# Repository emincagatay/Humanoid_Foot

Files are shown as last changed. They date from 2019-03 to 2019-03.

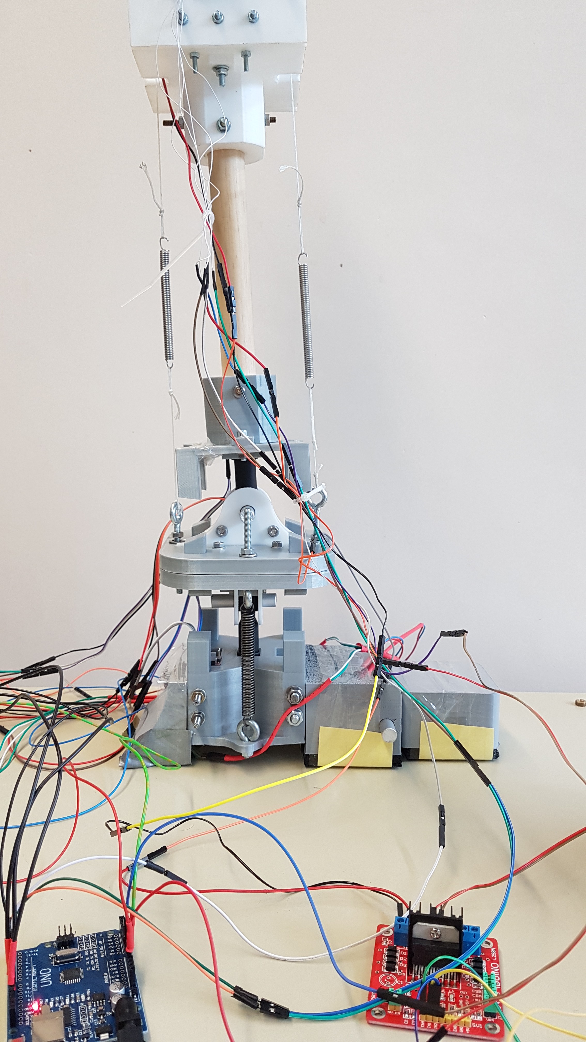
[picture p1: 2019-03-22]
Pictures/20180824_173448.jpg

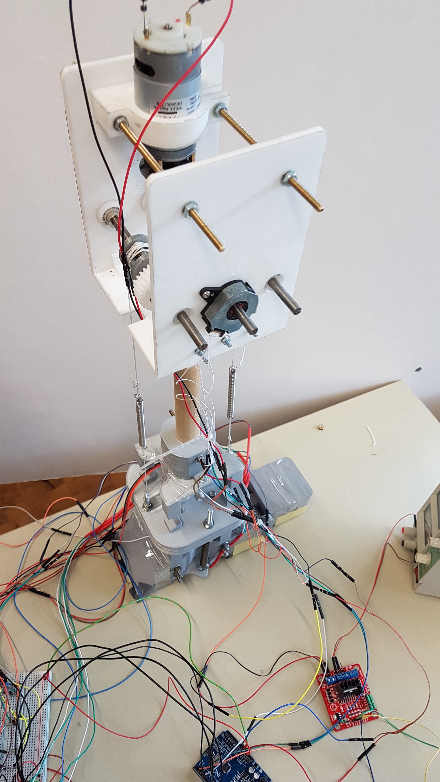
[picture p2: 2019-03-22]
Pictures/20180824_173456.jpg

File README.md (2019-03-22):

# Humanoid_Foot
Humanoid Foot Demonstrator

The project was a team project and has been completed by the team during the second semester of my Master's degree. Our project was a part of a bigger project which is the design and production of th every part of a humanoid robot and assemly of these parts. The goal of our project is the provide a starting point for a years long project. Every year new teams are asked to improve the previous version of the design. After the desired level is achieved, all parts of the robot will be assembled to form a complete humanoid robot. 

Necessary explanations can be found in the PDF-Document titled "Final Documentation for the humanoid foot demonstrator of Group 2".

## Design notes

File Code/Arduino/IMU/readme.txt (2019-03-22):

This code works with the teensy 3.6 with 3 MPU 9250 on 3 different i2c Pins with 4.7k pull up resistors. It prints the roll pitch yaw from the Earth->Sensor Transformation to the serial connection to be read by either the serial monitor/Simulink running on C/Simulink running on the Pi.
Its mostly self written but contains parts from https://github.com/arduino-ibraries/MadgwickAHRS , https://github.com/kriswiner/MPU9250 and https://github.com/nox771/i2c_t3

Interesting functionalities:
There is a I2c Scanner method which can be used to check the I2c network for devices (useful for debugging purposes). The code also includes a send2Simulink method which is used to send data to Simulink to be read via its serial read. Serial.print does not work with simulink!! But its necessary for the serial monitor. Outside of this the code should be self explanatory. If not check the sources and githubs provided for more information.

Possible Code Improvements: 
MultiThreading. currently we ask get values from one sensor before we ask the next. This process involves waiting on sensor response->multiple threads to increase efficiency
general code quality(eg enums,std::array/std::vector, etc.)
optimization for speed
EEPROM to save calibration values: currently calibration values are entered directly in the code  
Add some more method especially to access sensor setup from the main. Might be handy

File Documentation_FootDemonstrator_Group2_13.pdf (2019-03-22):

Group 2 | Humanoid foot Demonstrator | Hamburg, 26.08.2018

### Final Documentation for the humanoid foot demonstrator of Group 2

This document provides vital information and installation guides of all implemented components used in the humanoid foot. The functionality of the foot is simplified to one active pitch movement controlled with a dc motor a passive roll movement and a passive roll movement of the toes. The foot movement is detected with three IMUs, in addition an encoder is used to record rotation after the gearbox and force sensors are used to detect ground contact. The overall control is done witch a Simulink model run on a raspberry pi. The sensor data is processed with an Arduino Uno.

### Table of content

### Design

### Tasks distribution

The following table gives a brief overview of the task distribution in our group, after the design process was done.

TASK
ASSEMBLY & TESTING | Christian Brendes, Doruk Utkan, Emin Nakilcioglu, Kevin Deutmarg, Marvin
| Gravert, Stephan Hansen, Till Staude
CAD-DESIGN | Doruk Utkan, Emin Nakilcioglu, Till Staude
ENCODER | Till Staude
FORCE SENSOR | Stephan Hansen
IMU | Marvin Gravert
MOTOR CONTROL | Christian Brendes, Kevin Deutmarg
REFERENCE SIGNAL | Gunnar Maerker
SIMULINK MODEL | Christian Brendes, Kevin Deutmarg, Marvin Gravert, Stephan Hansen, Till
| Staude

### Requirement list

The requirement list was the result of an iterative design process and the base for assumptions and calculations in the part design/selection process. For further information take a look in our midterm presentation “20180518_HumRob_Midterm”.

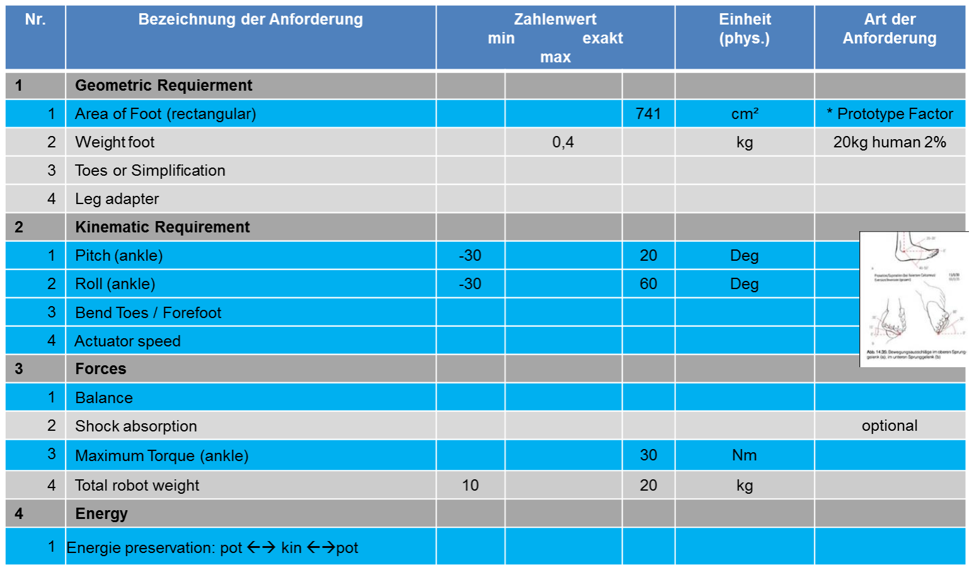
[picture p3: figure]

## Humanoid foot demonstrator Group 2

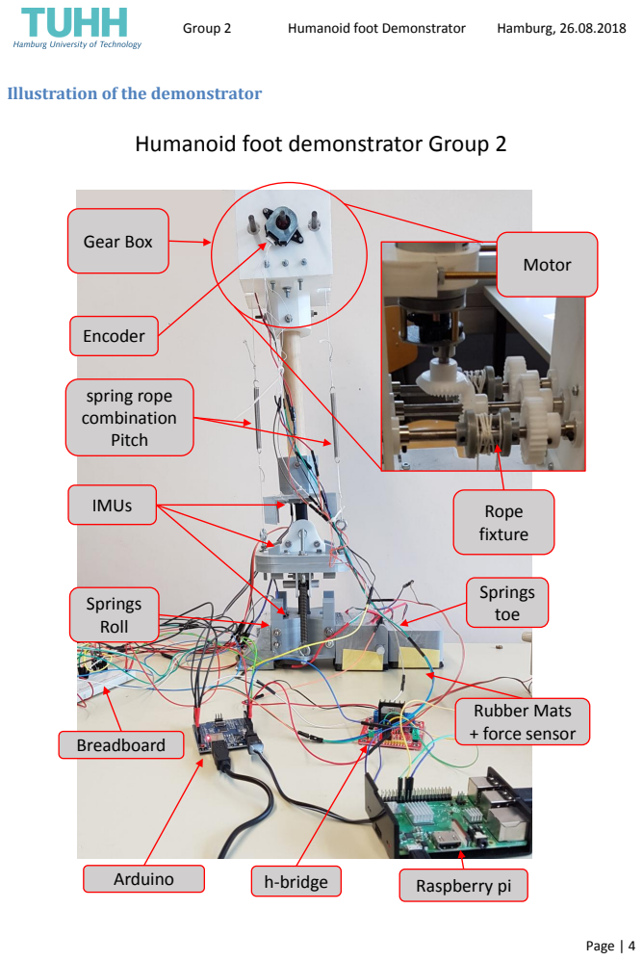
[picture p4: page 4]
Rubber Mats + force sensor; Springs Roll; spring rope combination Pitch; Encoder; Gear Box; IMUs; Breadboard; Raspberry pi Arduino; h-bridge; Motor; Rope fixture; Springs toe

Illustration of the demonstrator

### Hardware part list

The following list shows the implemented parts for this demonstrator.

Partname | Function
Raspberry Pi 3 B+ | Microcontroller for the motor control setup
H-Bridge, Iduino L298N | DC motor controller
Arduino Uno R3 | Microcontroller for processing sensor data
Teensy 3.6 | Microcontroller for processing IMU data
12V DC Motor | Actuator for the demonstrator
1x Encoder | Detect rotation of rope fixtures
3x IMUs (MPU9250) | Detect roll and pitch movement of foot
4x Interlink force sensors | Detect ground contact
2x Spring tilt
2x Spring roll
2x Spring toe
1x Bevel gear
3x Spur gear
1x A/D converter MCP3008
2x Amplifier LM 393P
Rubber mat | Adding some damping to ground contact
IGUS bearings (no. BB-626-B180-30-ES, GSR-06,
KBRM-10 OK, GBM-10, GSR-10, GFM-101115-03)
12V Power Supply Unit | Power supply for the DC motor
1x Breadboard | Used for quick wiring
RJ45 Cable, USB AtoB cable
Wires, Resistor … | Additional electrical components
Steel shaft, screws, … | Mechanical components for assembly

### Assembly Instructions for the current state

The foot is stored half-assembled right now. All small wires are connected and most mechanical parts are in place. If you want to put the foot together, only the following steps are needed:

Mechanical Assembly
- put together the bearing and shaft for pitch
- attach roll springs, tight the screws such that roll is in balance
- attach pitch springs, tight the screws that pitch is in balance
Electronic Assembly
- connect the Arduino to the Raspberry via USB (B to A) using the upper left USB port
- connect the Teensy to the Raspberry via USB (Micro-B to A) using the lower left USB port
- connect the Arduino and Raspberry to their power supplies
- connect the H-bridge to a power supply (12V)
- connect the Raspberry via Ethernet to your PC running Simulink

### Exploded view of the CAD Model

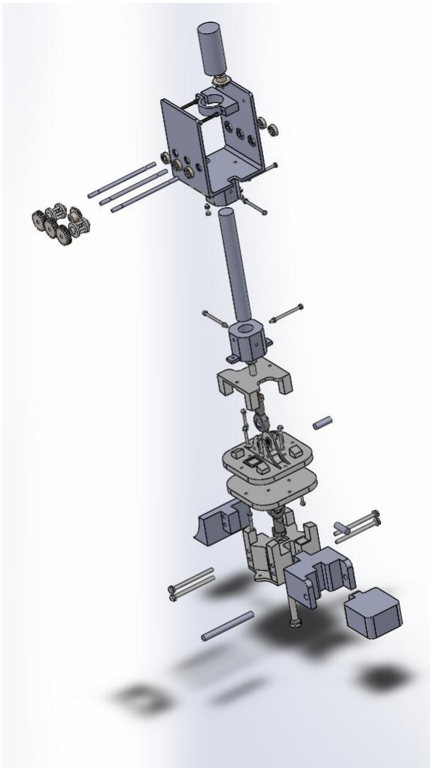
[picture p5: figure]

### Model for Pitch Behavior

We created a simple model for the pitch behavior which may help as a start for control purposes.Please find the illustrations and calculations in a separate file: Attachment_Pitch_Model.docx

The model has not been tested in further detail but it has been implemented in matlab/Simulink and can be found in the folder Attachment_Pitch_Model

### Selection of components

### Selection of Roll Springs (Extension Springs)

Aim: Find springs such that the roll of up to +/-30° happens with relatively little resistance (1-2Nm) estimated by body weight and leverage when ground contact is not centered below the foot. [I’d recommend to reestimate the value in a next iteration]

Link to shop:
https://www.febrotec.de/content.php?seite=shop/produkte.php&details=16226&hauptrubrik=23

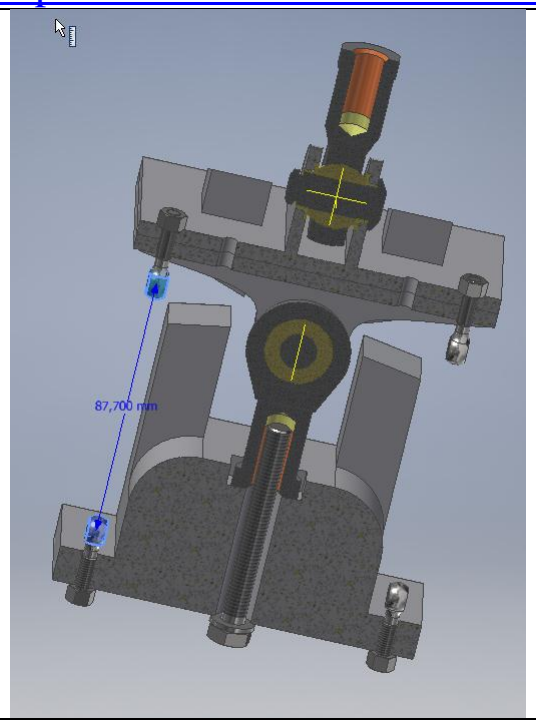
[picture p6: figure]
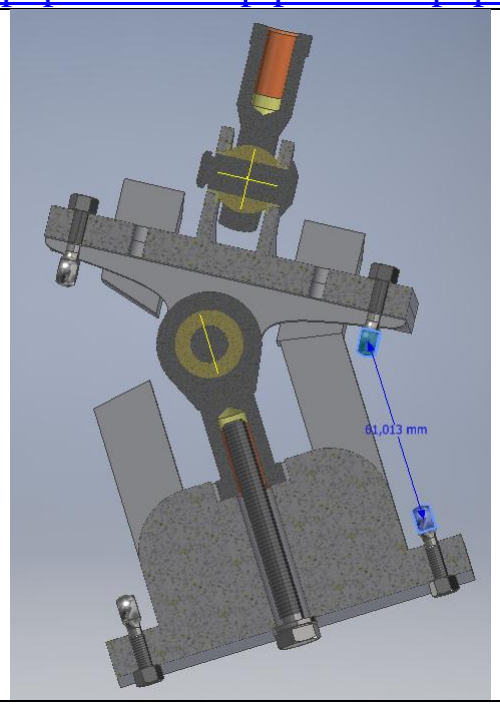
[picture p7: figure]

Zero Position | At 30° (max angle) | At -30° (min angle)
Spring length over angle | Force in spring over angle | Moment of both springs about rotation axis over angle → see what angle is achieved by which external moment

Find in files: RollSpringDiagram.mlx → Code for calculations

### Selection of Pitch Springs (Extension Springs)

For selected spring rotation of motor (beta) and pitch angle (alpha) and corresponding moment over pitch axis. (These values are independent of the roll angle!)

Note: We selected rather hugh springs as we initially planned to support big moments which may be necessary for walking (30/40 Nm). During the design we finally assumed our prototype would not manage the big pretension forces caused by these springs, so finally they were not used. For the next iteration in design, either design a more stable component (problem: expensive, harder to manufacture) or choose smaller springs and assume smaller load values (i.e. moments).

Find in files: PitchSpringDiagram.mlx → Code for calculations

Troubleshooting:
The selected (and bought) springs were way too massive to be implemented in the current system, since the prototype could probably not withstand the loads assumed for a full (child sized) human. So we did finally decide to not use the spring but users we got in the workshop. In the next iteration change the size of the components (some were oversized, others were too small) to fit the expected loads.

### Selection of Actuator

To select a suitable actuator for the pitch movement initial calculation were necessary to get a number for the motor power and rotational speed. The following table contain the Power calculation of our motor. Therefore simplified assumptions of the overall dimensions of our foot design were made, illustrated in Figure 1.

Foot Moment | 30 Nm -> requirement list
Foot Mass | 3000 g (see figure .. for dimension) | Density 1.5 g/cm³ 3D-Printer Material
Inertia | = 0.0275 kg*m²
Spring Force | 30 Nm / 0.05m = 600N

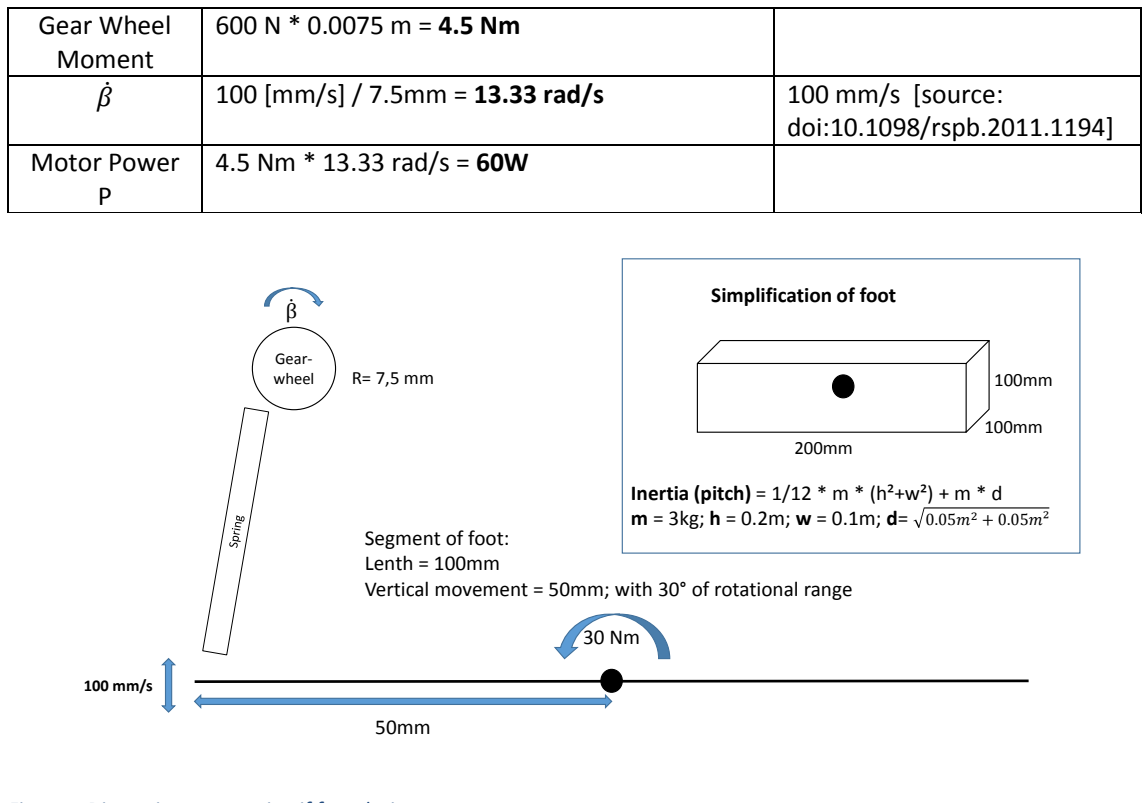
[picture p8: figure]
Gear-; wheel; Segment of foot: Lenth = 100mm; Simplification of foot

Gear Wheel Moment | 600 N * 0.0075 m = 4.5 Nm
β̇ | 100 [mm/s] / 7.5mm = 13.33 rad/s | 100 mm/s [source: doi:10.1098/rspb.2011.1194]
Motor Power P | 4.5 Nm * 13.33 rad/s = 60W

Figure 1 Dimension assumption if foot design

With this rather conservative calculation we come to the solution that we require 60W of Motor Power. The following internet search for a suitable motors concluded we have to lower the requirements for the motor to fit it in to our budget of 300€

If we lower our torque requirement from 30 Nm to 15Nm and also changing and change our speed from 100mm/s to 50mm/s we end up with a gear moment of 2,25Nm and 63,6RPM. That is almost in the range of the following motor! (Hochleistungsgetriebemotor 12 V Modelcraft RB350050-22723R 50:1 https://www.conrad.de/de/hochleistungsgetriebemotor-12-v-modelcraft-rb350050-22723r-501-233132.html (https://www.conrad.de/de/hochleistungsgetriebemotor-12-v-modelcraft-rb350050-22723r-501-233132.html) )

Vertical movement = 50mm; with 30° of rotational range

Inertia (pitch) = 1/12 * m * (h²+w²) + m * d m = 3kg; h = 0.2m; w = 0.1m; d=

### Design Process of the Gearbox, Toes and Heel

Gearbox includes a motor mount, a framework, 6 ball bearings, 1 bevel gears set, 3 spur gears and 2 winders. Taking into account the torque that needs to be transferred, the modules of the gears, diameter of the shafts and dimensions of the ball bearings have been calculated. Bevel gears and spur gears requires the module of at least 0,58 and 0,8, respectively.

Determining the Shaft Diameter
Torsion occurred on the shaft by DC Motor;

P = 1 ,18 W , n = 44,18 rp (taken from the DC motor catalogue considering the torque of 3,28 Nm)

τb1 =

16 ∗ M1
π ∗ d1

3 ≤ τem = 72 MPa

M1 = 9

P
n

= 3,28 N

d1

3 ≥

16 ∗ 3,28
π ∗ 72

→ d1 ≥ 2,8

Forces acting on the spur gears;

Ft2 = Ft3 =

2 ∗ T
d

= 218,6 N

Fr2 = Fr3 = Ft ∗ tan α = 79, 6 N

Forces acting on the bevel gears;

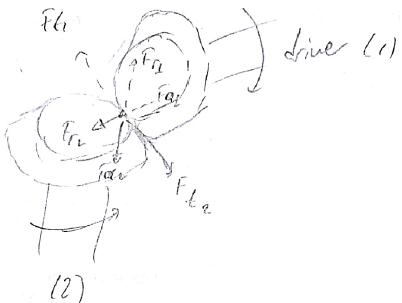
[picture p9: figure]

Reference cone angles (δ1, δ )= 45°, helix angle (β )= 0° ,shaft angle(∑) = 90°

pressure angle (α) = 20° , face width(b) = 7 mm , dm= reference diameter angle

dm1 = 31 − 7 ∗ sin δ1 = 26,

dm2 = 31 − 7 ∗ sin δ = 26,

Ft1 = Ft2

Ft1 =

2 ∗ T dm
= 218,6 N

Fr2 = Fa1 = Ft ∗ tan α ∗ sin δ = 64,81 N

Fr1 = Fa2 = Ft ∗ tan α ∗ cos δ = 64,81 N

a = 33,7 | , b = 16 | , c = 14,3

Mtorsion = 3,28 N

Mbending = Mx = −Fr2

∗ (a | b | 18) Fa2
∗ 26, | ≈ −2,7 N

According to the maximum shear stress theory;

Meq = √Mt
Mb

2
= 4,24 N

d1

3 ≥

32 ∗ Meq
π ∗ τem

→ d1 ≥ 3,91

6 mm has been decided as the shaft diameter considering the safety factor of 1,5.

After these calculations, we have bought gears made of Polyacetal, which meets the design criteria, silver shafts with 6 mm diameter and ball bearing with plastic cage material and balls made of stainless steel. Winders which plays the active role in the transmission was designed in the shape of a cylindrical cage so that during the assembly rope could have been easily fixed onto one of the bars regardless of the initial position of the winder. Framework, motor mount and the winders has been printed using 3D Printer.

The toes and heel parts are connected to lower adapter part in a way that lower adapter part is a bit elevated from the ground. There are 2 reasons for this setup: Main reason is to imitate the arc structure of the foot in human beings. Scientific papers show that the middle part of the foot has the lowest pressure while walking or standing and the most pressured points are the toes and heels. The second reason is due to the screws in the lower adapter part which should not contact to the ground as it would disturb the contact layer of the foot.2 torsional springs are used to imitate the bending of toes so that some of the energy can be restored and reused passively while walking.

Troubleshooting
The 3d printing process of toes and heels were a bit frustrating. At first trial 100% printing density was used but the parts were too heavy for the motor to handle. At second trial 30% is used but this time the quality of the parts was poor therefore the parts had to be reprinted many times which is very frustrating and suffering since the printing time was quite long and the student workshop was unexpectedly closed some days during the course of the semester.

### Actuator - 12V DC Motor

This is the installation guide our human foot demonstrator. This part provides the installation steps for creating a DC motor control with an H-Bridge and Raspberry Pi 3 B+ and MATLAB Simulink R2018a. It covers the following:

- Used hardware part list
- Schematic of all components
- Flashing procedure of the Pi with MATLAB OS
- Network configuration for communication setup
- Manual for the motor control MATLAB script
- Manual for the motor driver in Simulink

### Used hardware part list

The following list shows the used parts for this motor setup for this demonstrator.

Partname | Function
Raspberry Pi 3 B+ | Microcontroller for the motor control setup
H-Bridge, Iduino L298N | DC motor controller
12V DC Motor | Actuator for the demonstrator
12V Power Supply Unit | Power supply for the DC motor
Breadboard | Used for quick wiring
Breadboard cables | Connectors for quick wiring
3x LEDs | Used for indicating the current status of the motor (turn left, turn right, stop)
Micro USB Power Supply Unit | Power cord for the microcontroller
RJ45 Cable, 1m | Network cable for connecting Pi with PC
3x resistors | Required for the lowering the input voltage of LED

### Schematic of all components

The schematic of the demonstrator is straight forward. Pi 3 B+ we use the following GPIO pin layout as reference.

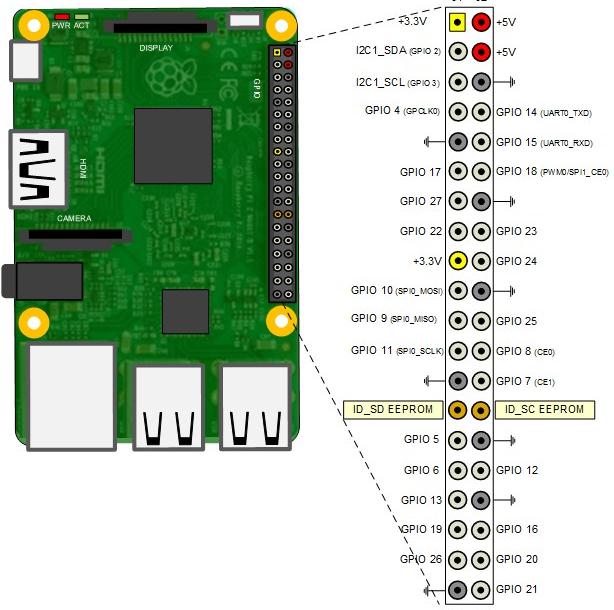
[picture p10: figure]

Figure 2 MATLAB showPins layout for Pi Model 3 B

From the Pi we use ground and map it on the breadboard for our LED monitoring. The LEDs need a dropping resistor otherwise the LED would break, since the output voltage of the GPIO pins are 3.3V and the permitted voltage for LEDs we have used is 1.6V. Constants:

UGPIO = 3 3 V

IGPIO = 16 A

ULED = 2 V

RV =

UGPIO − ULED

IGPIO

=

3 3 V − 1 6 V
16 A

= 1 6 2 Ω

Therefore, we chose the next bigger available resistor which has a resistance of 110 Ω.

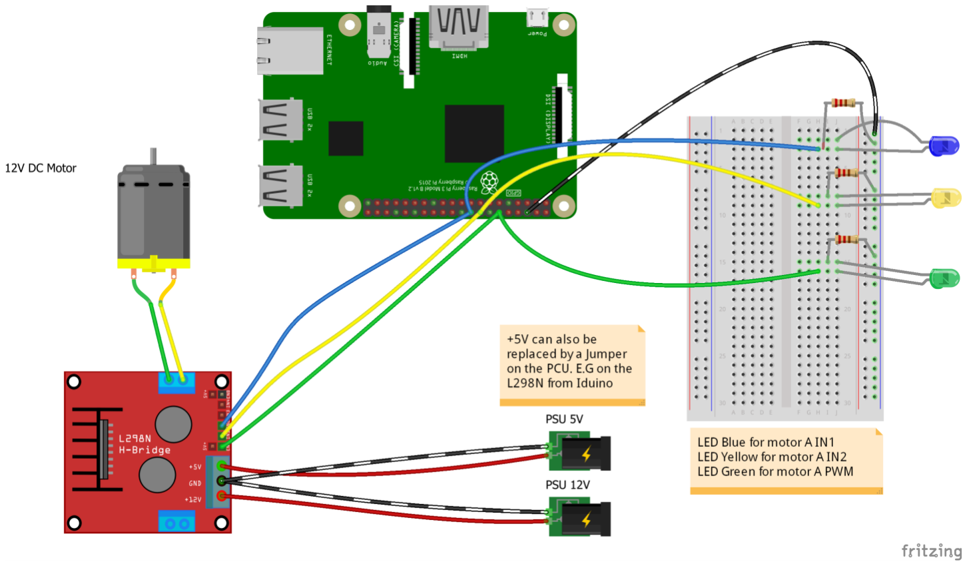
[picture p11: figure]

Figure 3 Fritzing Breadboard Diagramm for Motor Control

From the Pi we connect the breadboard LED control with series resistors. Use therefore ground, GPIO 18 for green, GPIO 23 for yellow and GPIO 24 blue.

Next we connect the Pi with the H-Bridge. Simply connect the GPIO 18 to Enable A (EnA control for motor A, we could control also two motors with this bridge). This allows us the control the motor speed with Pulse Width Modulation (PWM). Then connect GPIO 23 for IN2 and 24 for IN3.

In order to understand the way of controlling the motor we visualize the small motor control.

InA | InB | Motor movement
0 | 0 | Stop
0 | 1 | Left
1 | 0 | Right
1 | 1 | Stop
Table 1 Motor Control

Now we hook up the motor by using the corresponding motor pins for voltage and ground. Since we have a DC motor it doesn’t matter in with order we connect power or ground, it only affects the way of turning the motor. So be consistent and test afterwards which way the motor is turning depending on your input of InA and InB.

Lastly we need to connect power to the H-bridge. Depending on the purchased model a jumper will be shipped. The purpose of the jumper is to use 5V of the 12V power needed for the motor to supply the onboard components of the bridge with power to work properly. If you remove the jumper you need to attach a separate 5V power supply to power up the board and additional 12V for the motor power supply.

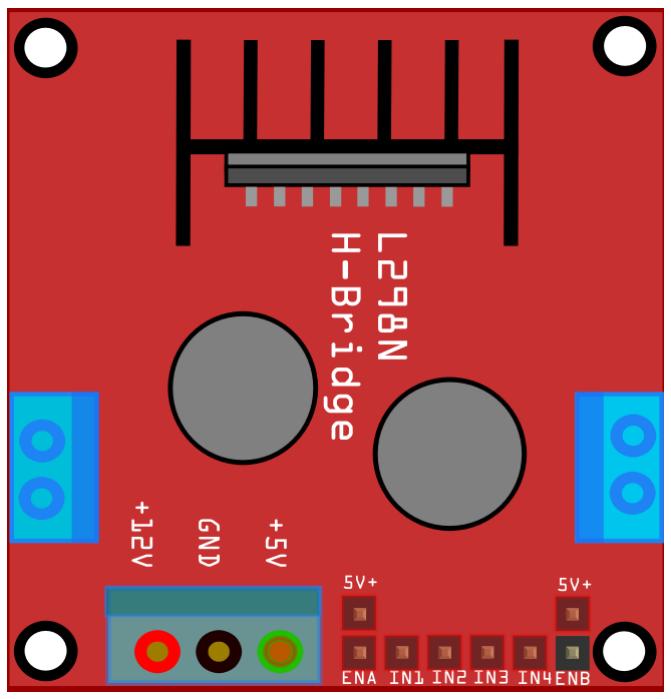
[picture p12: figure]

Figure 4 H-Bridge

Troubleshooting
Depending on the used power supply, place the jumper to power on the board, otherwise the board won’t receive signals from the microcontroller.

### Sensors

This section gives a brief description of the implemented sensors

### Encoder

The Encoder (AMT31 by CUI INC) is used to read the angle of the middle gear shaft. This corresponds (1:1) to the motor angle (behind the gear which is purchased with the motor). The connector “JAE FI-W17S” was not easily available, so we build our own, only connecting to pins 4,6,8,10,12, corresponding to GND, +5V, B+, A+, Z+.

The following Figure 5 gives the wiring and the corresponding pins

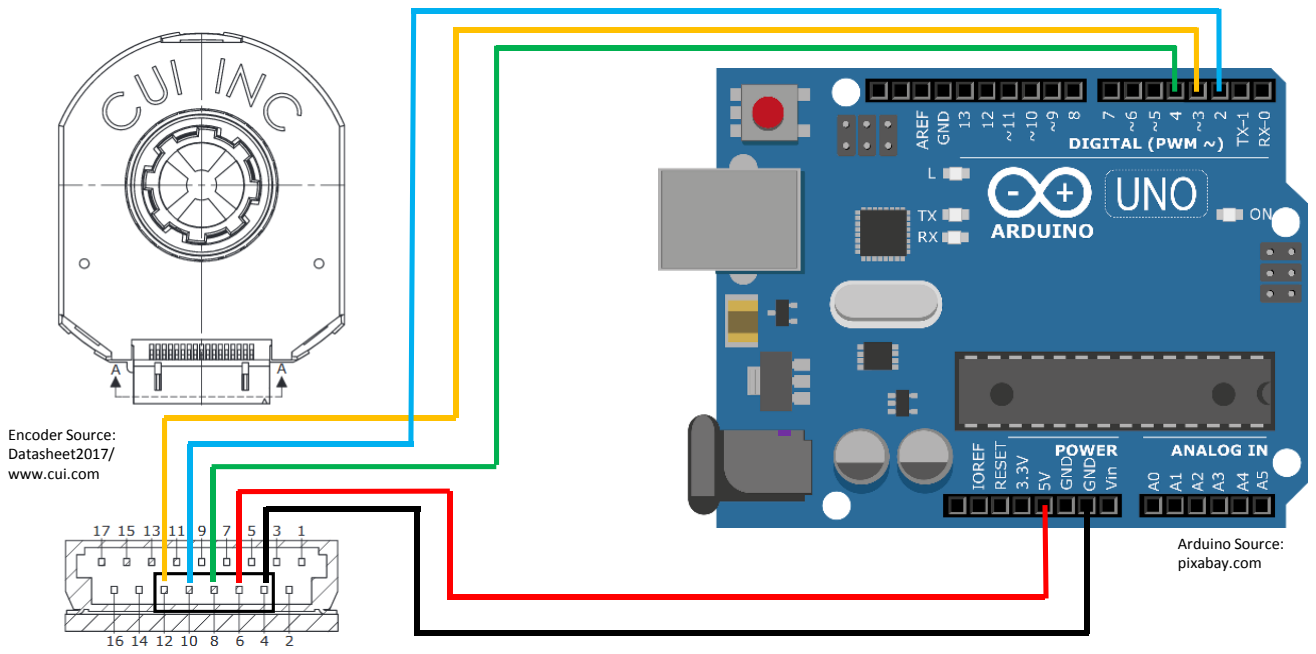
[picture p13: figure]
Arduino Source: pixabay.com; Encoder Source: Datasheet2017/ www.cui.com

Figure 5 Wiring Encoder Arduino

A & B form a quadrature signal. They are the same signal but shifted in time. If A lags behind be the rotation direction is the one way (say negative), if B legs behind A it is the other direction (say positive). There is four cases when a change in A (or B) was detected A=1 & B=0; A=0 & B=1 (both positive direction) and A=0 & B=1; A=1 & B=0 (both negative direction).

Z gives a pulse whenever a zero crossing happens.

As the encoder works incremental each signal flank of either A or B must be detected to correctly sum the steps to the angular value. The encoder resolution is 4096/round (so 2048 up and 2048 down flanks). Using Simulink for Raspberry Pi we could not read the data sufficiently fast (especially when other blocks like the motor control were included) thus we moved the encoder reading to a Arduino and only send the calculated angular value via a serial connection (USB).

To always reference to the same 0 position (given by Z signal) we initially turn the motor slowly until the first Z pulse is received, only after that that initialized bit is set and the actual code may start. (Note: make sure the motor is in the correct rotation, as this cannot be detected by the encoder and initially rotation 0 is always assumed.)

For the serial connection, set the correct Port in the Simulink Block, find the value by typing

ls /dev/tty*
in the command line on the paspberry pi (e.g using putty) and see which element is added when you connect the Arduino by USB.

Find in the files:

Data sheet of encoder; Code for Arduino

Troubleshooting:
The encoder seemed to “pass out” at times, we are not sure for the reason, but we did not even get a signal using an oscilloscope. Possible reasons may be: Bad connector, loose connection, insufficient power supply by the Arduino, bad quality of the encoder or anything else.

### Force Sensor

The force sensor (Interlink Drucksensor Force-Sensing Resistor FSR) are used to detect whether the foot is touching the ground or not. These sensors are passive elements exhibits a decrease in resistance when there is an increase in the force. The dimensions of the sensors are 18.3 x 0.46 mm(Ø x H) and have a working range from 0.2N – 20N. A typical resistance vs. force curve is shown in Figure 6 Force to Resistance and Voltage relationship of FSR; source: FSR® Integration Guide.

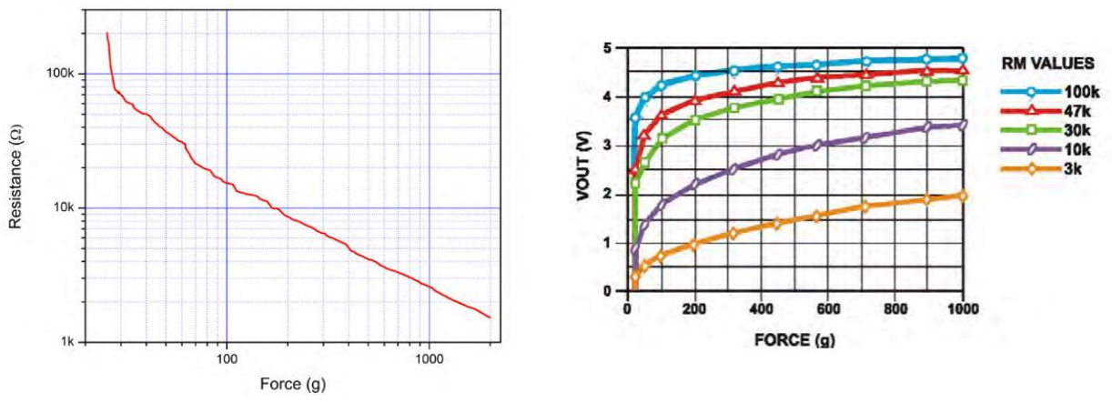
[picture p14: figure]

Figure 6 Force to Resistance and Voltage relationship of FSR; source: FSR® Integration Guide

The measurement setup is shown in Figure 7, a simple voltage divider circuit including the FSR Resistor is used. In the shown configuration, the output voltage increases with increasing force. The measuring resistor, RM, is chosen to maximize the desired force sensitivity range and to limit current. In our implementation RM is chosen as 57 kΩ. As amplifier the LM 393P is used, for further information check the data sheet (http://www.ti.com/lit/ds/symlink/lm393.pdf).

Figure 7

To convert the analog signal given by Vout to a digital signal the MCP 3008 is used. The MCP3008 device is a 10-bit Analog-to-Digital (A/D) converter with on-board sample and hold circuitry, it operates over a broad voltage range (2.7V - 5.5V). Our operation range is the 3.3V output from the Arduino Uno R3. The MCP 3008 has 8 input channel, we only need 4 channel, the wiring to the Arduino is shown in Figure 8. The communication is done via the spi interface. To read out channel 0-3 we followed the tutorial from Robert Fromm (http://www.robert-fromm.info/?post=elec_spi_mcp3008), also used his code.

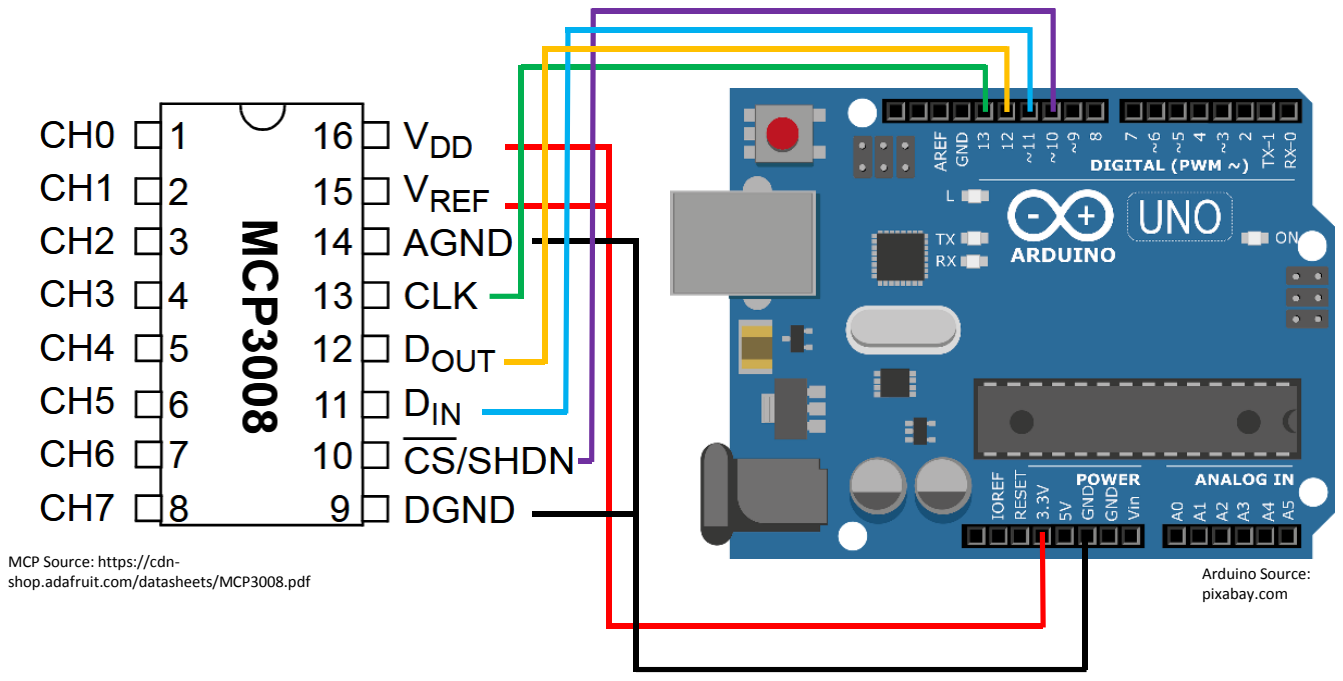
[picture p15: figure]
Arduino Source: pixabay.com; MCP Source: https://cdn-

Figure 8 MCP3008 to Arduino wiring

Vout

V (3,3V)

GND

Vout =

V
( | )

shop.adafruit.com/datasheets/MCP3008.pdf

Troubleshooting: To detect the ground contact more reliable a small paper was placed under the Force sensors

### IMU

Reason to use IMUs: For the control loop it is necessary to calculate the pitch and roll. This can obviously be achieved using encoders, but they are quite expensive. Therefore we wanted to try out the cheaper IMUs. They are used to calculate the roll pitch (yaw) between the earth frame and the sensor frame. This can in turn be used to calculate the relative angle between them.

For 1 DOF joints this is achievable with only 6 axis IMUs (gyroscope+accelerometer) assuming the sensor axis allign with the axis of rotation (or the transformation is known). For a more general and theoretically more robust method we decided on 9 axis IMU (also includes an magnometer).

Choice of Hardware: We decided to use the MPU9250 from Invensense due to its cheap price and its frequent use in the open source community, therefore offering a good basis in case of problems to fall back on. In the sources folder you find the product information, register map as well the orientation of the MPU.

Note that we didnt buy the MPU9250 directly but rather bought a breakout board for its ease of use.

To run the sensor fusion we orginally wanted to use a Raspberry Pi but run into some problems with simulink and first turned to the Arduino UNO. While we got the fusion (somewhat, see below) working for one sensor, we figured the UNO is still to slow to offer results in the acceptable range. Hence we used a Teensy 3.6. Its more than ten times faster than an UNO and offers 4 I2Cs Channels/Ports/Pins.

Senor Fusion: As already remarked we orginally thought of the using the Raspberry Pi. This would have probably resulted in quite a low sampling rate. Hence we looked for a sensor fusion still offering acceptable results at low rates who would also be computationally inexpensive. The fusion algorithm designed by Magdwick fits the pill (paper in sources, http://x-io.co.uk/open-source-imu-and-ahrsalgorithms/ ).

Calibration: In theory all individual sensors on the MPU9250 (acc, gyro, mag) have to be calibrated. In practise we have only calibrated the offset in the gyroscope(absolutly necessary) and the scaling error as well offset magnometer (absolutly necessary). For the first we simply took x amounts of samples while the gyros werent moved and averaged it to calculate the offset. The scaling error couldnt be calibrated, because we were lacking a reference angluar velocity. The magnometer calibration is very important. There exist quite a few ways to this. We went with a simple mapping as described here (https://github.com/kriswiner/MPU6050/wiki/Simple-and-Effective-Magnetometer-Calibration ). Most simple magnometer calibration rely on mapping ellipsoid measurements to a sphere (for one see sources). At this point its important to note that our magnometer wasnt well calibrated and we experienced poor performance due to it. So you would be well advised to look for other calibration methods.

Set Up: The Teensy is connected to the Raspberry/PC over a micro USB cable. The sensor are connected to the 3.3V and Ground of the teensy. Each indiviual IMU is connected to an I2c channel of the teensy. Furthermore 4.7k pull up resistors have to used (This is a must, otherwise you wont get readings).

Code: The code was written for the teensy but its close to known Arudino libaries. Its recommended to know some C++. Furthermore you will have to install teensyduino.

Performance: We had good results for the roll and pitch but pretty bad ones for the yaw. We believe this is due to the insufficient calibration.

Troubleshooting:

### Matlab/Simulink

### Flashing procedure of the Pi with MATLAB OS

There are two options to flash the SD card with the raspbian operating system including all packages from matlab.

Option 1 – Tutorial via Matlab

There exists a tutorial provided by Matlab to set up your raspberry pi. If this works great! otherwise turn

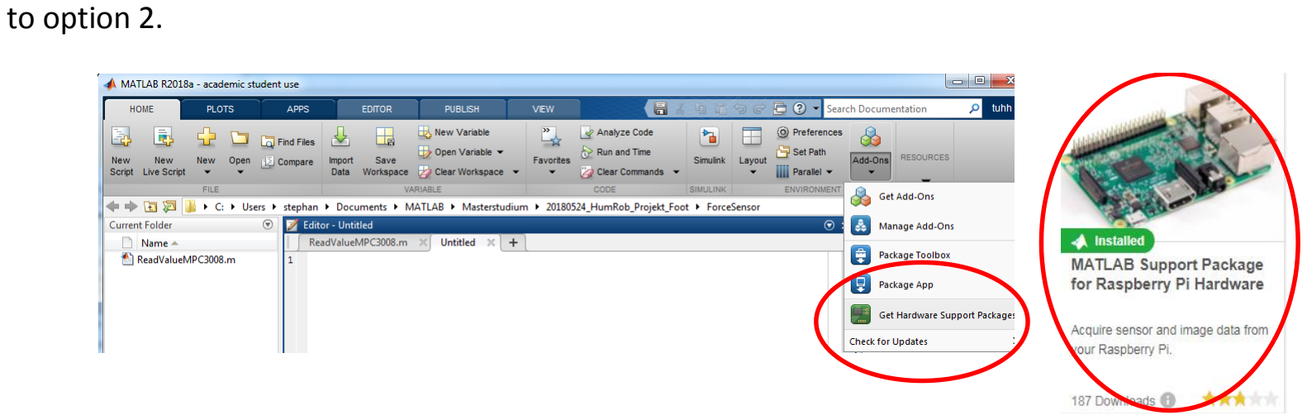
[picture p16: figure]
to option 2.

Note: The raspbian op provided by matlab was not bootable with the raspberry pi model 3b+

Option 2 – Manual installation

Firstly download the newest version of raspbian op
(https://www.raspberrypi.org/downloads/raspbian/), this should guarantee to work with your raspberry pi. Afterwards flash your SD card with the downloaded op (Hint: We used Win32 Disk Imager). Insert the SD Card in your pi and boot the op system. Make sure you have installed all updates, therefore enter sudo raspi-config into the console.

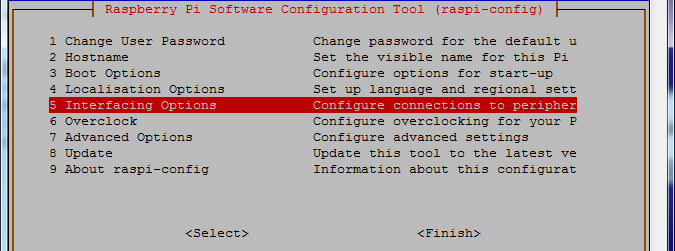
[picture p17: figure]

Abbildung 1 Source: https://learn.adafruit.com/adafruits-raspberry-pi-lesson-4-gpio-setup/configuring-i2c

Under 8.Advanced Options the raspberry pi can be updated. Afterwards reboot and install the missing matlab packages with the following command.

sudo apt-get install matlab-rpi

If the installation was successful run sudo raspi-config and select 5.Interfacing Options, enable ssh, i2c and gpio connection. Afterwards reboot your pi and connect it to your pc via a lan-cable. Make sure you know the IPaddress of your pi. Run sudo ifconfig to find the IP address next to the wlan0 entry. At last run the rasp(‘IP-Adress’,’user name’,’password’) command in matlab.

To verify the installation reinstall the Matlab Support Package for Raspberry Pi Hardware witch Matlab on an existing operating system.

Troubleshooting

If the installation of the matlab packages was not possible in one step there is the option to install the packages one by one. Also note you have to run the command rasp(‘IP-Adress’,’user name’,’password’) at least once before you can verify your installation with the “Matlab Support Package for Raspberry Pi Hardware”.

One by one installation: run the following command and replace the xxx with the listed package names

sudo apt-get install xxx

libsdl1.2-dev | alsa-utils | espeak | i2c-tools
libi2c-dev | ssmtp | ntpdate | git-core
v4l-utils | cmake | sense-hat | sox
libsox-fmt-all | libsox-dev | libcurl4-openssl-dev

### Network configuration for communication setup

During the flashing of the raspberry Pi one was asked to define a proper IP address to the PI. We have chosen: 169.254.0.2.

After that we need to hook up the PI with our PC using the Ethernet cable. Then we need to re-configure our network IPv4 address to: 169.254.0.10 / 255.255.0.0

Once this is done we can start Matlab to run our setup code.

### Manual for the motor control MATLAB script

As a pre-reqiusited for using matlab on raspberry pi you need to install the current support packages for matlab and Simulink, which can be easily found via Get Hardware Support Packages.

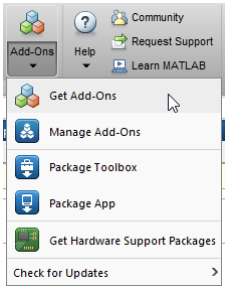
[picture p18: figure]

Then install Simulink support package for raspberry pi hardware and matlab support package for raspberry pi hardware.

Via installation follow the instructions of the install wizard and you good to go.

For the motor control we have set up a dedicated matlab script for initial testing. Within there we have placed additional comments for easy understanding of the functions from the MATLAB raspberry PI API.

An overview of the function used can be found on following link: https://de.mathworks.com/help/supportpkg/raspberrypiio/functionlist.html

### Manual for the motor driver in Simulink

Within Simulink we have created a motor control block which takes and input u which can be between [-1,1]. This input should come from another system block which provides new directives turning or stopping the motor. Output signals are pwm_out (for motor speed), mIn1_ and ,In2_out for the turning and stopping the motor.

The control scheme looks as follows:

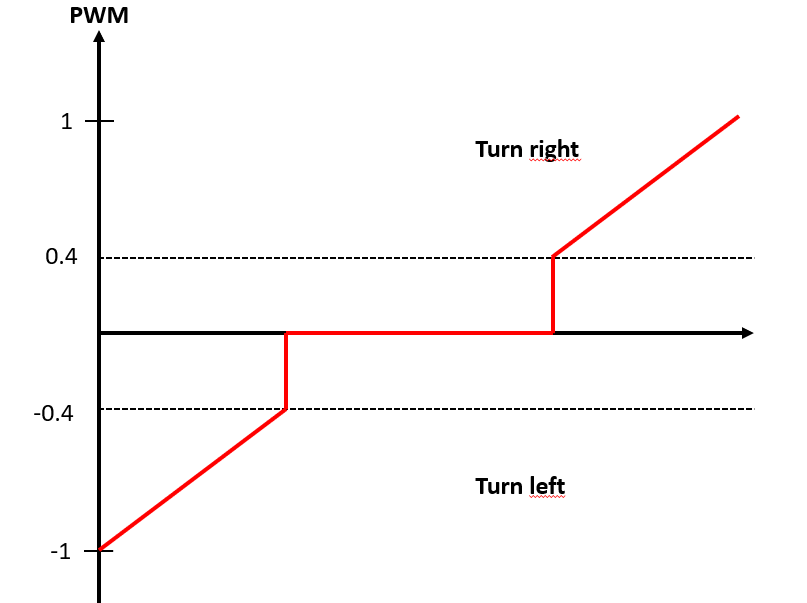
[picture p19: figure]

Before running the simulation check first if the simulation is selected to external. Otherwise you won’t be able to see anything in your scope when you would like to check some signals.

### Reference Signal for the ankle

According to Kwons and Parks paper "Kinesiology-based robot foot design for human-like walking." from 2012, the foot movement happens in four phases:
1. Standing (PHI = 0, foot has full ground contact)
2. Take-off (PHI > 0, PHI increases, foot has some ground contact)
3. Swing (PHI decreases, foot is in the air)
4. Landing (PHI < 0, PHI increases, foot has some ground contact) (This numbering conforms the one in Simulink.)

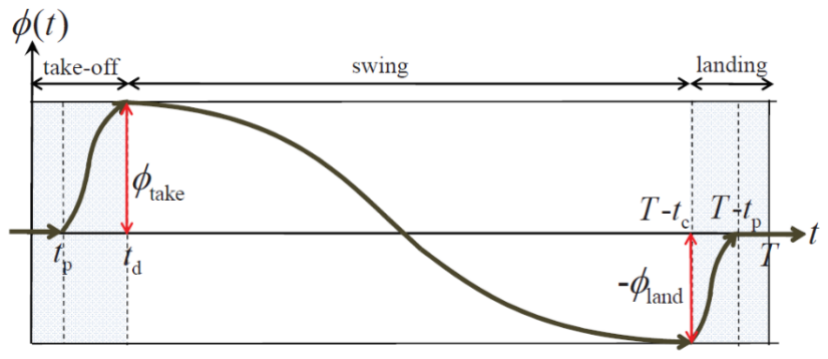
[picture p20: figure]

To be able to start off with slower movements, a scaling factor is used. If it’s set to one, T equals the suggested value of 2 seconds. The Simulink model which provides this curve looks like this:

The Time-Subsystem counts the time of a phase in seconds and provides it as a variable for the Function Subsystem, where the functions of all 4 phases are being calculated. The multiport switch then picks the right function based on the phase which is actually happening. This information comes from the phase no counter subsystem. For more insights look into the documentation of this.

### Overall Control Model

In the following segment some general remarks for the Simulink model for the demonstrator will be made. The model will be introduced in the following graphic.

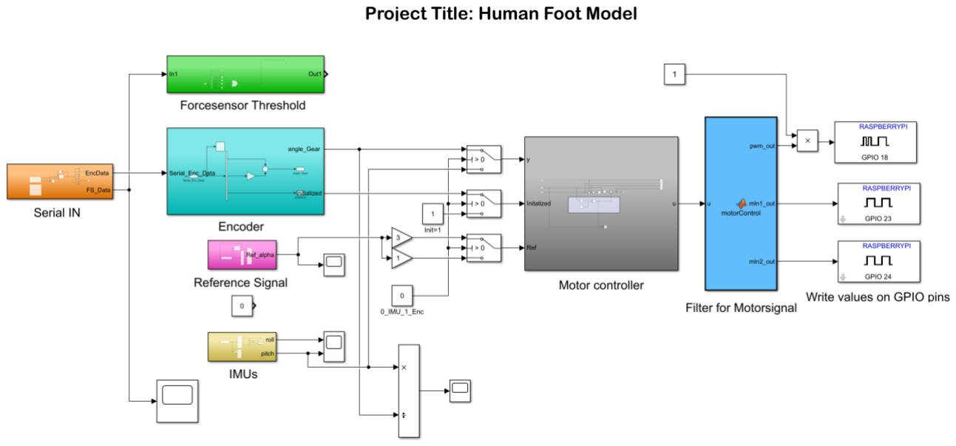
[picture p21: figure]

The model contains blocks to read out data from the different sensors, control the motor and to write the values of the motor controller onto the GPIO pins of the raspberry pi. It starts with a “Serial IN” block which is used to read out the data from the force sensors and the encoder (which are both preprocessed on the Arduino) over the USB port of the raspberry pi (connected to the Arduino). The block diagram looks as followed.

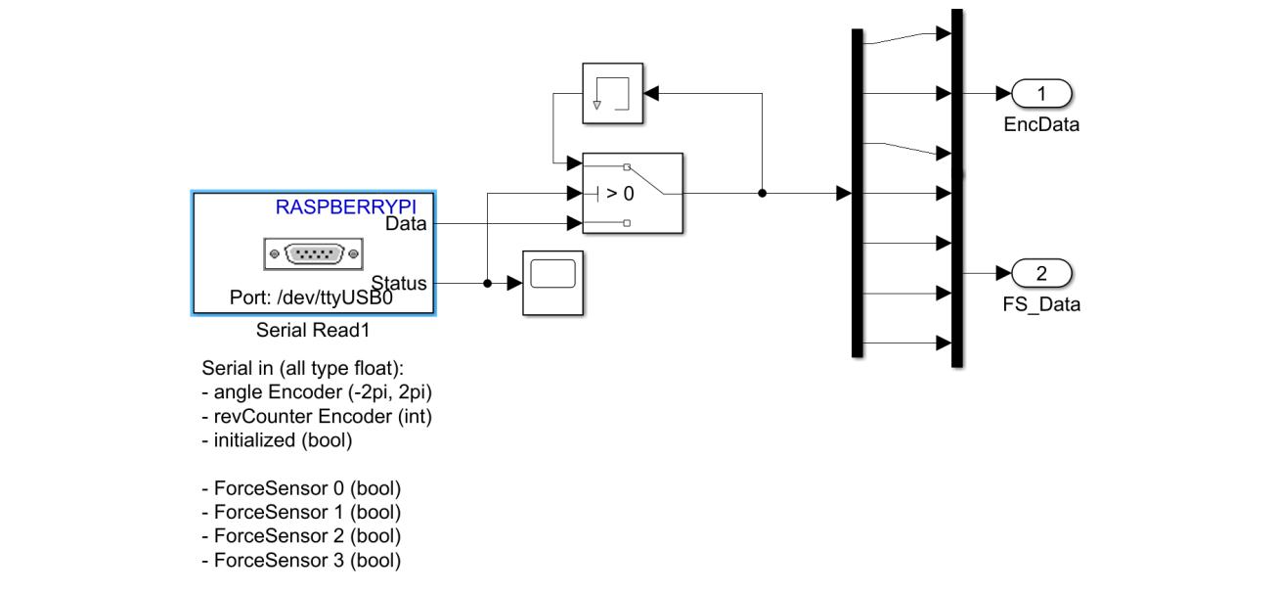
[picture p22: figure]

The “Serial IN” block is followed by the “Force sensor Threshold” and the “Encoder” blocks which are used to process the acquired data. The force sensors are so far only used to determine whether the foot touches the ground or not which is used to trigger the movement of the foot.

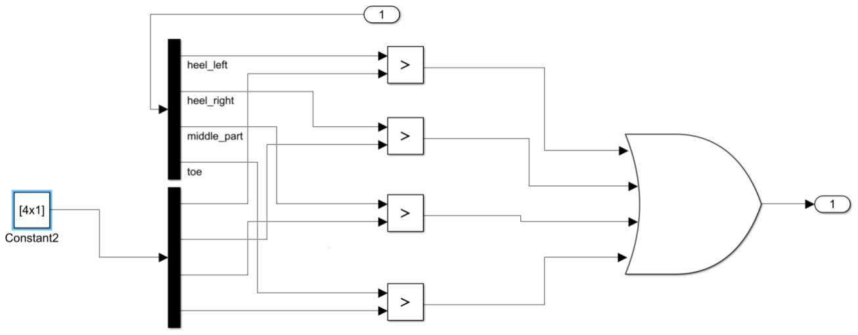
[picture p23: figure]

Here the input vector from the sensors gets demuxed and compared to a distinct value which is one since we are only detecting whether the foot is in contact with the ground or not. Therefore, if one of the sensors give a value greater than 1, the foot is in contact with the ground and the output of the block will be a logical 1 which is supposed to trigger the foot motion in future projects.

The “Serial IN” also delivers an input for the encoder block, which is illustrated in the following picture.

Here the collected data (see the previous Encoder section) will be demuxed. The data vector contains the following information:

1. The angle of the foot in an interval of (-2pi; 2pi)
2. The full revolutions counted (using the encoders Z signal)
3. A flag indicating if the encoder is initialized (i.e. at least one zero crossing was registered before)

The full angle is calculated by adding the current angle to the 2pi multiple of the revolution counter.

The reference signal block is described in the previous subchapter and additionally documented in the code.

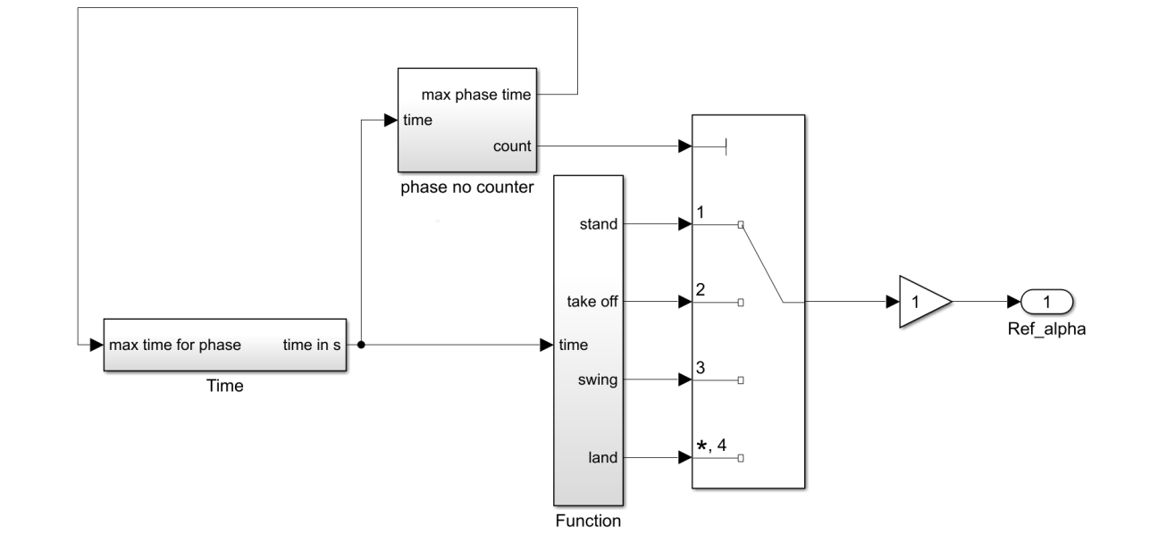
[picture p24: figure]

The reference angle has to be scaled before it gets fed into the motor controller.

The IMU block looks as followed.

It has its own “Serial IN” block which is used analogously to the previous “Signal IN” block to read out the data from the IMUs, which are preprocessed by the MPU9250.

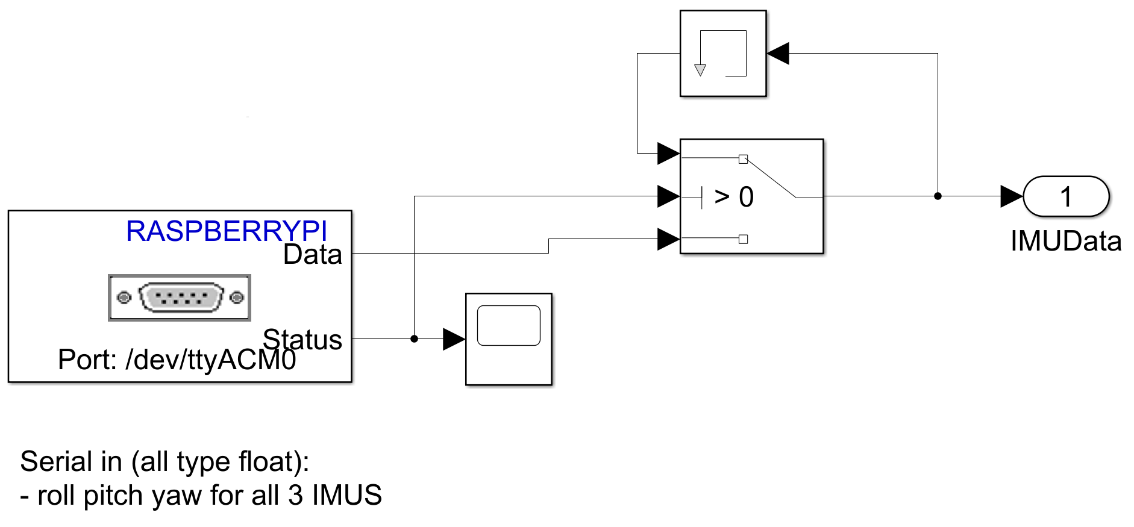
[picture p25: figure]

The input signal is processed in a function block, which outputs two angles (pitch and roll) for the motor controller.

Currently only one of the reference signals (either encoder or IMU angles) is used for control. A later state space model may use both simultaneously

The motor controller uses the processed sensor data of one of the two sensors and the reference signal as its input. In case the encoder is being used, the controller starts performing a slow initialization movement unless it’s initialized already. The control scheme which is implemented at the moment is a classical P-Controller, which compares the sensor signal with the reference. It will then feed the output values to the motor filter, which is described in the “Manual for the motor driver in Simulink section”.

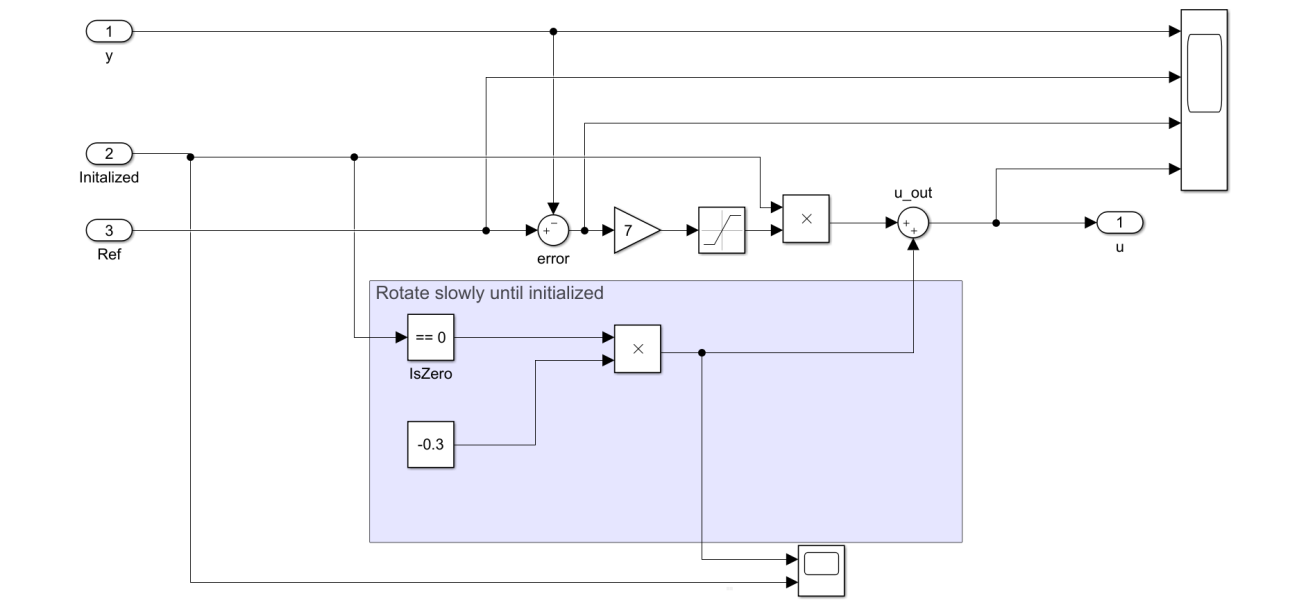
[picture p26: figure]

We used the following P values (sign depends on the direction in which the motor is mounted relative to the joints):

- Encoder based control P=-1
- IMU based control P = 5…7

After the signal got filtered the values get written on the GPIO pins of the raspberry pi which then actuates the foot.

### Outlook

Design
- Gears will jump if too much load is on the string which is connected on the barrell, use springs to preload the strings
- If you use 3d printer for parts use structure density of 30% due to reduced part weight
- Reduce the wooden shaft length in order to reduce weight and size of leg
- Build an external construction to lift the leg off the ground, otherwise one person needs to hold the leg up in the air which can be very exhausting

Microcontroller
- Do not use raspberry pi for the simulation. the matlab and simulink packages are not properly supported from mathworks, use arduino instead.

Force Sensor
- Filter Signal (e.g. low pass)

IMU
- Better calibration. Especially for the magnometer
- Switch to SPI, if i2c is bottlenecking your speed
- Try a different sensor fusion algorithm. Magdwick is fine if you only have limited processor speeds. The teensy offers more than enough therefore it might be sensible to switch to a more computational intensive fusion who provides higher accuracy

Reference Signal
- Add Triggers & Feedback from other leg to make real walking possible

Sole
- Material was not suitable for a good fixing on 3D-Printed parts. Use different material

### Appendix

### Shopping list

Raspberry PI 3 B+ All-In-Bundle | https://www.reichelt.de/Einplatinen-Computer/RASP-3-B-ALL-IN/3/index.html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 (https://www.reichelt.de/Einplatinen-Computer/RASP-3-B-ALL-IN/3/index.html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)
jumper cable | https://www.reichelt.de/Entwicklerboard-Zubehoer/DEBO-KABELSET/3/index.html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 (https://www.reichelt.de/Entwicklerboard-Zubehoer/DEBO-KABELSET/3/index.html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)
breadboard | https://www.reichelt.de/Experimentier-Steckboards/STECKBOARD-1K2V/3/index.html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 (https://www.reichelt.de/Experimentier-Steckboards/STECKBOARD-1K2V/3/index.html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)
Lan cable | https://www.reichelt.de/Patchkabel-Netzwerkkabel-Cat-5-e-/GOOBAY-73072/3/index.html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 (https://www.reichelt.de/Patchkabel-Netzwerkkabel-Cat-5-e-/GOOBAY-73072/3/index.html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)
DC-Motor | https://www.conrad.de/de/hochleistungsgetriebemotor-12-v-modelcraft-rb350050-22723r-501-233132.html (https://www.conrad.de/de/hochleistungsgetriebemotor-12-v-modelcraft-rb350050-22723r-501-233132.html)
Motor Controller (L298N) | https://www.conrad.de/de/motortreiber-motor-driver-board-1525437.html (https://www.conrad.de/de/motortreiber-motor-driver-board-1525437.html)
Bevel gear | https://www.conrad.de/de/polyacetal-kegelrad-reely-modul-typ-10-anzahl-zaehne-30-30-1-pckg-1515602.html (https://www.conrad.de/de/polyacetal-kegelrad-reely-modul-typ-10-anzahl-zaehne-30-30-1-pckg-1515602.html)
Spur Gear | https://www.conrad.de/de/polyacetal-stirnzahnrad-reely-modul-typ-10-bohrungs-o-6-mm-anzahl-zaehne-30-1515593.html
Silver steel shaft | https://www.conrad.de/de/silberstahl-welle-reely-o-x-l-6-mm-x-500-mm-237086.html
A/D Converter | https://www.conrad.de/de/datenerfassungs-ic-analog-digital-wandler-adc-microchip-technology-mcp3008-ip-extern-pdip-16-651456.html (https://www.conrad.de/de/datenerfassungs-ic-analog-digital-wandler-adc-microchip-technology-mcp3008-ip-extern-pdip-16-651456.html)
rubber mat | https://www.conrad.de/de/anti-rutsch-matten-l-x-b-x-h-20-cm-x-10-cm-x-8-mm-petex-43710104-regupol-7210-ls-plus-uv-lichtbestaendig-natriumchlor-1594087.html
IMU | https://www.exp-tech.de/sensoren/beschleunigung/7511/sparkfun-imu-breakout-mpu-9250 (https://www.exp-tech.de/sensoren/beschleunigung/7511/sparkfun-imu-breakout-mpu-9250)
Encoder | https://www.mouser.de/ProductDetail/CUI/AMT312S-V?qs=sGAEpiMZZMsWp46O%252bq11WX0VmCXIU00qD2iPTVNV8 yQ%3d (https://www.mouser.de/ProductDetail/CUI/AMT312S-V)
Interlink force sensor | https://eckstein-shop.de/Interlink-Drucksensor-Force-Sensing-Resistor-FSR-402-02-N-20-N-183-x-046-mmR-x-H (https://eckstein-shop.de/Interlink-Drucksensor-Force-Sensing-Resistor-FSR-402-02-N-20-N-183-x-046-mmR-x-H)
Spring tilt | https://www.febrotec.de/content.php?seite=shop/produkte.php&details=16671&hauptrubrik=23 (https://www.febrotec.de/content.php?seite=shop/produkte.php&details=16671&hauptrubrik=23)
Spring roll | https://www.febrotec.de/content.php?seite=shop/produkte.php&details=16226&hauptrubrik=23 (https://www.febrotec.de/content.php?seite=shop/produkte.php&details=16226&hauptrubrik=23)

spring toe | https://www.federnshop.com/en/products/torsion_springs/t-
| 19206l.html

### Arduino Code

// include the library code: #include <LiquidCrystal.h> #include <SPI.h>

typedef union
{
float number;
uint8_t bytes[4];
} FLOATUNION_t;

const uint8_t CS = 10; // Cock PIN SPI const double pi = 3.14159;

// PINs Encoder
const int pinA = 2;
const int pinB = 4;
const int pinZ = 3;
const int resolution = 4096/(2*pi);

// dynamic Values
double angle = 0; //[-2pi, 2pi] double revCounter = 0;
bool initialized = false;
bool toogle = false;

// Serial Communication
void send2Simulink(float tt) { FLOATUNION_t fa;
fa.number = tt;
for (int i = 0; i<4; i++)
{
Serial.write(fa.bytes[i]); }
}

// Called at every resolution step void change_A(){
if (initialized)
{
bool A = digitalRead(pinA); bool B = digitalRead(pinB);

if ((A && !B ) || (!A && B)) { angle += 1.0/resolution;
}else{
angle -= 1.0/resolution;
}

}

if (toogle){
digitalWrite(LED_BUILTIN, HIGH); }else{
digitalWrite(LED_BUILTIN, LOW); }
toogle = !toogle;
}

// Called whenever full 2pi are passed void rise_Z(){
if (angle > pi){
revCounter +=1;
}else if(angle < - pi){
revCounter -= 1;
}else{
//Do nothing as no full revolution assumed }

// Reset Angle to zero
angle = 0.0;

initialized = true;

}

// From http://www.robert-fromm.info/?post=elec_spi_mcp3008uint16_t mcp3008_read(uint8_t channel) {
digitalWrite(CS, LOW);
SPI.transfer(0x01);
uint8_t msb = SPI.transfer(0x80 + (channel << 4)); uint8_t lsb = SPI.transfer(0x00); digitalWrite(CS, HIGH);
return ((msb & 0x03) << 8) + lsb;
}

float forceSensor_Evaluator(uint16_t value){

return (float)value;
// uint16_t threshold = 80;
//
// | if (value < threshold){
// | return 0.0;
// | }else{
// | return 1.0;
// | }
}

void setup() {
| //Serial Communication
| Serial.begin(230400);

// SPI ################
SPI.begin();
SPI.setClockDivider(SPI_CLOCK_DIV8);

pinMode(CS, OUTPUT);
digitalWrite(CS, HIGH);

// #### ENCODER ###################################### pinMode(pinA, INPUT);
pinMode(pinB, INPUT);
pinMode(pinZ, INPUT);

attachInterrupt(digitalPinToInterrupt(pinA), change_A, CHANGE); attachInterrupt(digitalPinToInterrupt(pinZ), rise_Z, RISING);

pinMode(LED_BUILTIN, OUTPUT);

digitalWrite(LED_BUILTIN, HIGH); }

void loop() {
// SPI Force Sensor
float reading_F0 = forceSensor_Evaluator(mcp3008_read(0)); float reading_F1 = forceSensor_Evaluator(mcp3008_read(1)); float reading_F2 = forceSensor_Evaluator(mcp3008_read(2)); float reading_F3 = forceSensor_Evaluator(mcp3008_read(3));

// Encoder SEND
send2Simulink(angle);
send2Simulink(revCounter); send2Simulink(initialized);

// FORCE Sensor Send
send2Simulink(reading_F0); send2Simulink(reading_F1); send2Simulink(reading_F2); send2Simulink(reading_F3);

delay(100);

}

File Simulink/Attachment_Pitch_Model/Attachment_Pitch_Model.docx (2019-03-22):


Back Side | | | | Front Side

Length of Rope + Spring
s_b | = l_b^β +l_b^S +l_b^α +l_b^0 | | | s_f | | = l_f^β +l_f^S +l_f^α +l_f^0
| =-β_b r_b +(F_b)/(k_b)+sin(α)d_b +l_b^0 | | | | | =-β_f r_f +(F_f)/(k_f)+sin(α)d_f +l_f^0
⇒c_b | =-β_b r_b +(F_b)/(k_b)+sin(α)d_b =const | | | ⇒c_f | | =-β_f r_f +(F_f)/(k_f)+sin(α)d_f =const
⇒F_b | =k_b *(c_b + β_b r_b -sin(α)d_b ) | | | ⇒F_f | | =k_f *(c_f + β_f r_f -sin(α)d_f )

Condition - ∑M_0 =0
αI_0 | | =T_a -F_b d_b cos(α)+F_l d_f cos(α)
⇒g(α, β_b , β_f ) | | =T_a -k_b *(c_b + β_b r_b -sin(α)d_b )d_b cos(α)+k_f *(c_f + β_f r_f -sin(α)d_f )d_f cos(α)- αI_0 =0
| | =T_a - αI_0 +cos(α)[k_f d_f (c_f +β_f r_f )-k_b d_b (c_b +β_b r_b )]+sin(2α)(k_b d_b^2 -k_f d_f^2 )=0

Gear Ratio (direction already considered to be opposing)
h(β_b ,β_f ) | | =β_b -nβ_f =0 | | | n=(β_b)/(β_f)

Kinetic Energy
T | | =1/2I_0 α^2 +1/2I_b β_b ^2 +1/2I_f β_f ^2

Potential Energy
V | | =-sin(α)mgh+1/2k_b (l_b^s )^2 +1/2k_f (l_f^s )^2
| | =-sin(α)mgh+1/2k_b (c_b + β_b r_b -sin(α)d_b )^2 +1/2k_f (c_f + β_f r_f -sin(α)d_f )^2

Euler Lagrange Equation

L =T-V+λ g(α, β_b , β_f )+μ h(β_b ,β_f )

(∂L)/(∂x_i)-d/(dt)(∂L)/(∂x_i)=Q_i
x_i ={α,β_b ,β_f } | | | Q_i ={T_a , T_b ,T_f }

T_a : external Torque applied to foot (result from external forces); T_b ,T_f : Torques applied by motor/gear

Assumptions:

- Angle of rope is so small that effect can be neglected (angle between rope in zero and non-zero position)
- Mass of spring + rope neglectable
- Zero position “orthorgonal” to gravity; else include extra angle in Potential energy

(∂L)/(∂α) | =(∂T)/(∂α)-(∂V)/(∂α)+λ(∂g)/(∂α)+μ(∂h)/(∂α)
| =cos(α)mgh+k_b (c_b + β_b r_b -sin(α)d_b )cos(α)d_b +k_f (c_f + β_f r_f -sin(α)d_f )cos(α)d_f
| + λ[-sin(α)[k_f d_f (c_f +β_f r_f )-k_b d_b (c_b +β_b r_b )]+2cos(2α)(k_b d_b^2 -k_f d_f^2 )]
(∂L)/(∂β_b) | =(∂T)/(∂β_b)-(∂V)/(∂β_b)+λ(∂g)/(∂β_b)+μ(∂h)/(∂β_b)
| =-k_b (c_b + β_b r_b -sin(α)d_b )r_b -λcos(α)k_b d_b r_b +μ
(∂L)/(∂β_f) | =(∂T)/(∂β_f)-(∂V)/(∂β_f)+λ(∂g)/(∂β_f)+μ(∂h)/(∂β_f)
| = -k_f (c_f + β_f r_f -sin(α)d_f )r_f +λcos(α)k_f d_f r_f +μn
d/(dt)(∂L)/(∂α) | =I_0 α
d/(dt)(∂L)/(∂β_b) | =I_b β_b
d/(dt)(∂L)/(∂β_f) | =I_f β_f

Equations of Motion
I_0 α | =cos(α)mgh+k_b (c_b + β_b r_b -sin(α)d_b )cos(α)d_b +k_f (c_f + β_f r_f -sin(α)d_f )cos(α)d_f + λ[-sin(α)[k_f d_f (c_f +β_f r_f )-k_b d_b (c_b +β_b r_b )]+2cos(2α)(k_b d_b^2 -k_f d_f^2 )]+T_a | (1)
I_b β_b | =-k_b (c_b + β_b r_b -sin(α)d_b )r_b -λcos(α)k_b d_b r_b +μ+T_b | (2)
I_f β_f | = -k_f (c_f + β_f r_f -sin(α)d_f )r_f +λcos(α)k_f d_f r_f +μn+T_f | (3)

(2)→ | μ | = I_b β_b +k_b (c_b + β_b r_b -sin(α)d_b )r_b +λcos(α)k_b d_b r_b -T_b | | (4)
(3)+(4)→ | I_f β_f | = -k_f (c_f + β_f r_f -sin(α)d_f )r_f +λcos(α)k_f d_f r_f +nI_b β_b +nk_b (c_b + β_b r_b -sin(α)d_b )r_b +λncos(α)k_b d_b r_b -nT_b +T_f | | (5)
(5)→ | λ(cos(α)k_f d_f r_f +ncos(α)k_b d_b r_b ) | | = I_f β_f +k_f (c_f + β_f r_f -sin(α)d_f )r_f -nI_b β_b -nk_b (c_b + β_b r_b -sin(α)d_b )r_b +nT_b -T_f | (6)
(6)→ | λ | =(I_f β_f +k_f (c_f + β_f r_f -sin(α)d_f )r_f -nI_b β_b -nk_b (c_b + β_b r_b -sin(α)d_b )r_b +nT_b -T_f)/(cos(α)(k_f d_f r_f +nk_b d_b r_b )) | | (7)
(1)+(7)→ | | Final equation to find α=f(α,β_b ,β_b ,β_f ,β_f ,T_a ,T_b ,T_f )

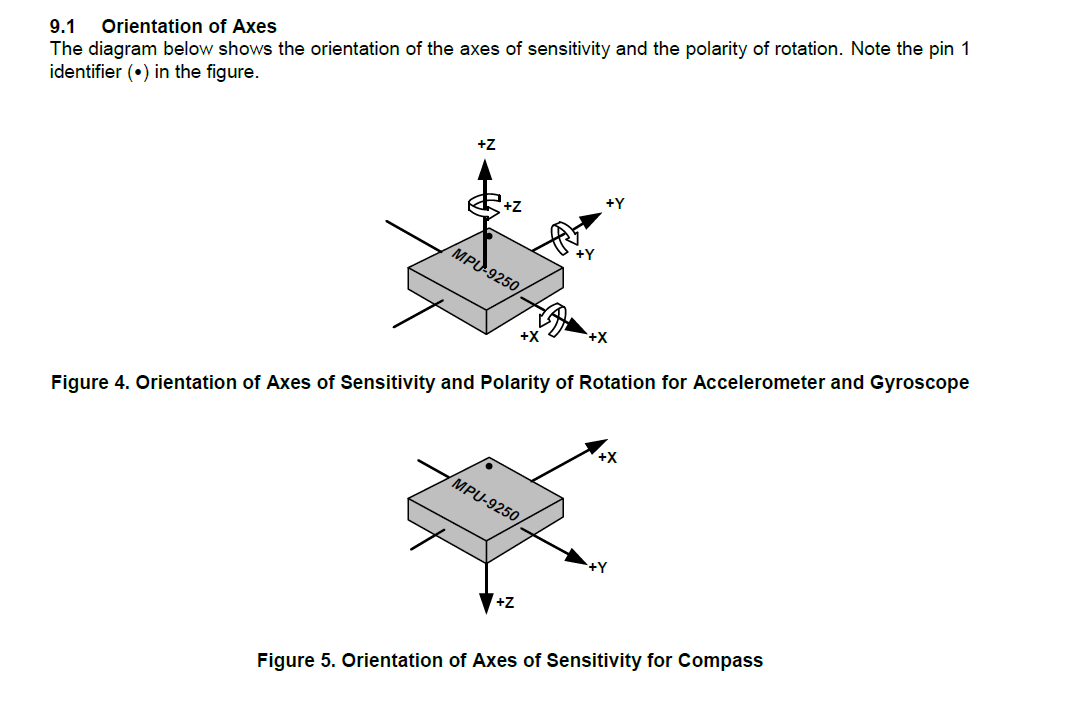
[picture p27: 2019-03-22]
Data-Sheets/IMU/orientationMPU9250.PNG

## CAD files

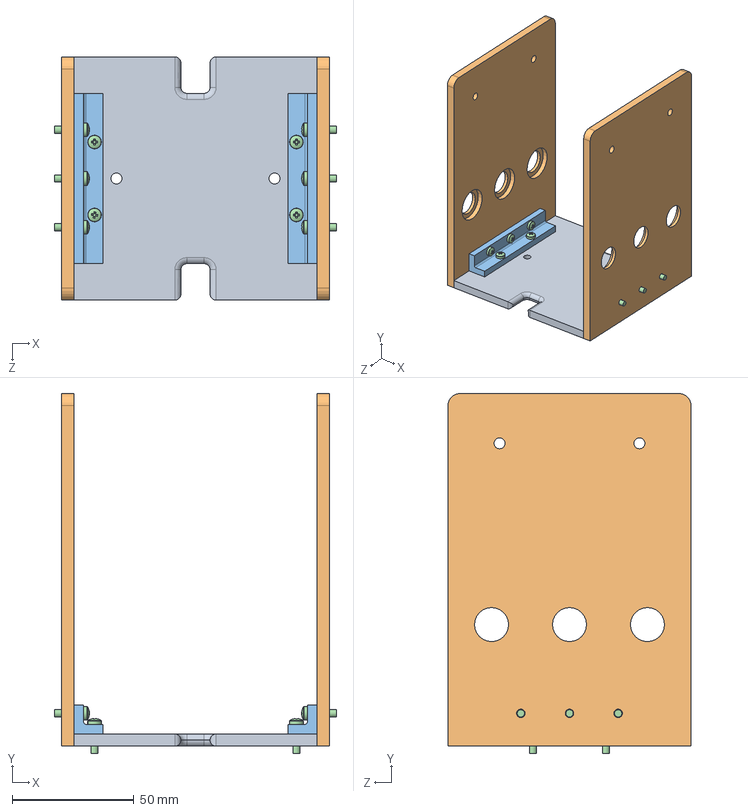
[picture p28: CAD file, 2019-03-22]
CAD/Gearbox/Spare_framework/Spare_framework.SLDASM
116.0 x 148.0 x 100.0 mm
Framework3
framework2 x 2
bracket x 2
pan head cross recess screw_din x 10

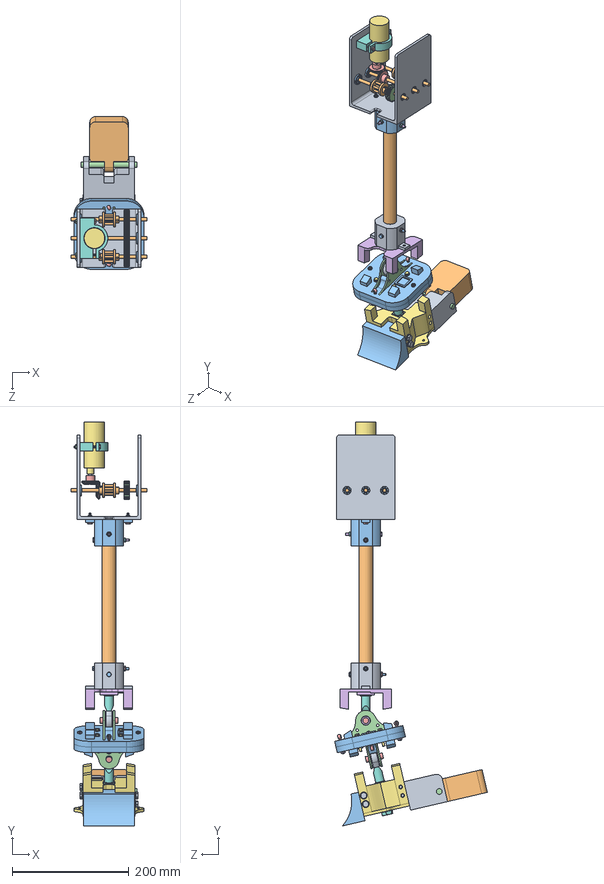
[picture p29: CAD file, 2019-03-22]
CAD/Full_assembly.SLDASM
130.0 x 691.4 x 261.5 mm
Framework
Shaft x 3
angular contact ball bearing_68_iso x 6
spur gear_iso x 3
straight bevel gear_iso x 2
snap ring-type a-for shafts_din x 6
DC_Motor
Motor_Mount
Motor_Shaft_out
Winder x 2
Wood_Connection
hex thin nut gradeb_iso x 4
hex screw gradeab_iso x 4
Long_screw x 2
Plain_washer_M4 x 2
Nut_M4 x 2
Sick_Adapter
Mid_WoodShaft
DIN 933 - M4 x 60 x 2
DIN 433 - 4,3 x 4
DIN 934 - M4 x 2
Upper_Adapter
DIN 933 - M10 x 25
Fork_Base x 2
Fork_Side x 4
joint_shaft x 2
gleitlager x 4
Lower_Adapter
DIN 933 - M10 x 65
Print_Hindfoot
Toe_shaft
Eye bolt GB 798 M4 x 30 x 4
ISO 4032 - M4 x 4
DIN 933 - M4 x 28 x 4
DIN 125 - A 4,3 x 4
DIN 933 - M6 x 80 x 4
DIN 126 - 6,6 x 4

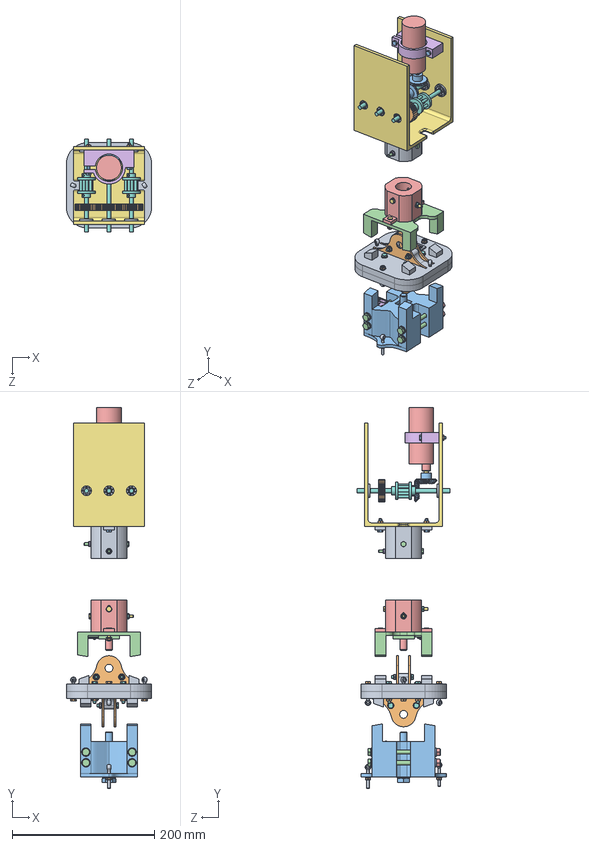
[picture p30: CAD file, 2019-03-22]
CAD/Assembly_ank+gear.SLDASM
120.0 x 535.4 x 130.0 mm
Fork_Base x 2
Fork_Side x 4
Lower_Adapter
Upper_Adapter
Sick_Adapter
DIN 125 - A 4,3 x 26
DIN 933 - M4 x 16 x 2
DIN 933 - M4 x 28 x 9
Eye bolt GB 798 M4 x 30 x 6
ISO 4032 - M4 x 12
DIN 126 - 6,6 x 8
DIN 933 - M6 x 80 x 5
ISO 4033 - M6 x 4
DIN 433 - 4,3 x 4
DIN 933 - M4 x 60 x 2
DIN 934 - M4 x 2
DIN 555-5 - M4 x 4
DIN 433 - 10,5
DIN 933 - M10 x 65
DIN 125 - A 10,5
DIN 933 - M10 x 25
SparkFunMPU-9250 x 3
Framework
Shaft x 3
angular contact ball bearing_68_iso x 6
spur gear_iso x 3
straight bevel gear_iso x 2
snap ring-type a-for shafts_din x 6
DC_Motor
Motor_Mount
Motor_Shaft_out
Winder x 2
Wood_Connection
hex thin nut gradeb_iso x 4
hex screw gradeab_iso x 4
Long_screw x 2
Plain_washer_M4 x 2
Nut_M4 x 2

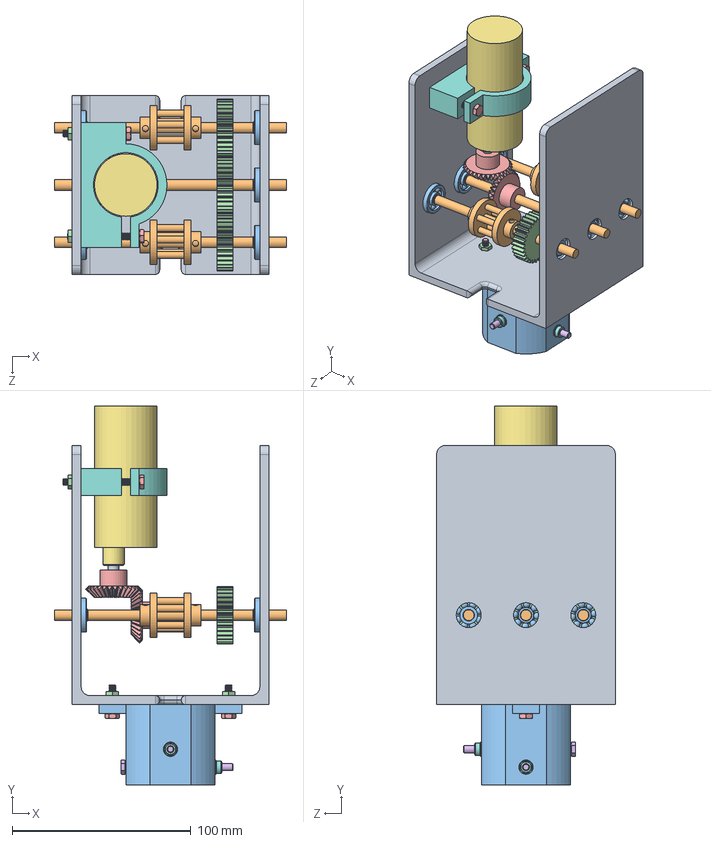
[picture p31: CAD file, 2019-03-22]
CAD/Gearbox/Assem_Motor_Gearbox.SLDASM
130.0 x 212.0 x 100.0 mm
Framework
Shaft x 3
angular contact ball bearing_68_iso x 6
spur gear_iso x 3
straight bevel gear_iso x 2
snap ring-type a-for shafts_din x 6
DC_Motor
Motor_Mount
Motor_Shaft_out
Winder x 2
Wood_Connection
hex thin nut gradeb_iso x 4
hex screw gradeab_iso x 4
Long_screw x 2
Plain_washer_M4 x 2
Nut_M4 x 2

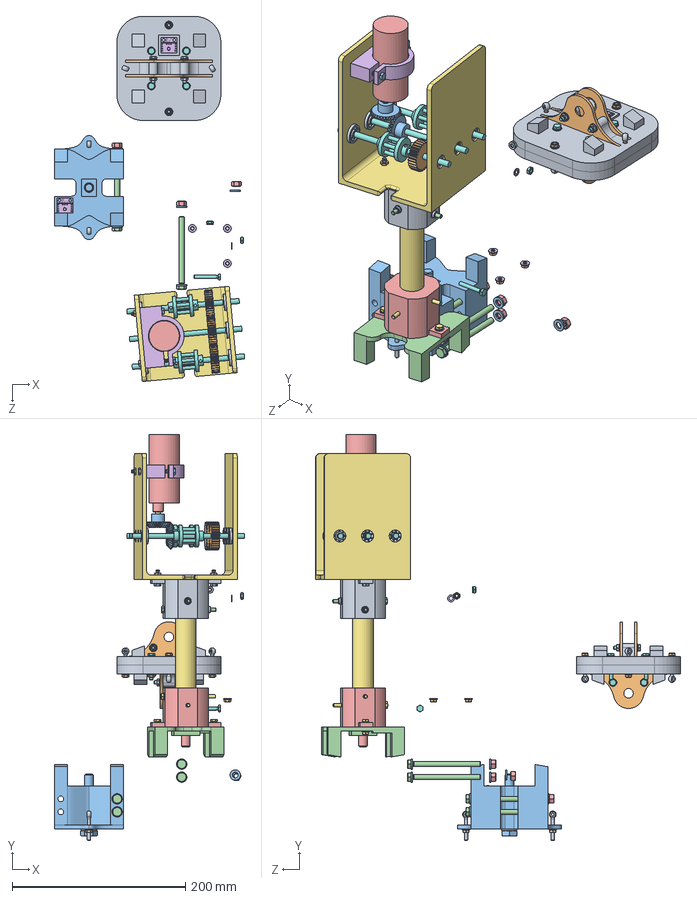
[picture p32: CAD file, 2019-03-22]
CAD/Ankle/Assembly_Ankle.SLDASM
219.5 x 468.0 x 421.0 mm
Fork_Base x 2
Fork_Side x 4
Lower_Adapter
Upper_Adapter
Sick_Adapter
DIN 125 - A 4,3 x 26
DIN 933 - M4 x 16 x 2
DIN 933 - M4 x 28 x 9
Eye bolt GB 798 M4 x 30 x 6
ISO 4032 - M4 x 12
DIN 126 - 6,6 x 8
DIN 933 - M6 x 80 x 5
ISO 4033 - M6 x 4
DIN 433 - 4,3 x 4
DIN 933 - M4 x 60 x 2
DIN 934 - M4 x 2
DIN 555-5 - M4 x 4
DIN 433 - 10,5
DIN 933 - M10 x 65
DIN 125 - A 10,5
DIN 933 - M10 x 25
SparkFunMPU-9250 x 3
Framework
Shaft x 3
angular contact ball bearing_68_iso x 6
spur gear_iso x 3
straight bevel gear_iso x 2
snap ring-type a-for shafts_din x 6
DC_Motor
Motor_Mount
Motor_Shaft_out
Winder x 2
Wood_Connection
hex thin nut gradeb_iso x 4
hex screw gradeab_iso x 4
Long_screw x 2
Plain_washer_M4 x 2
Nut_M4 x 2
Middle_WoodPart

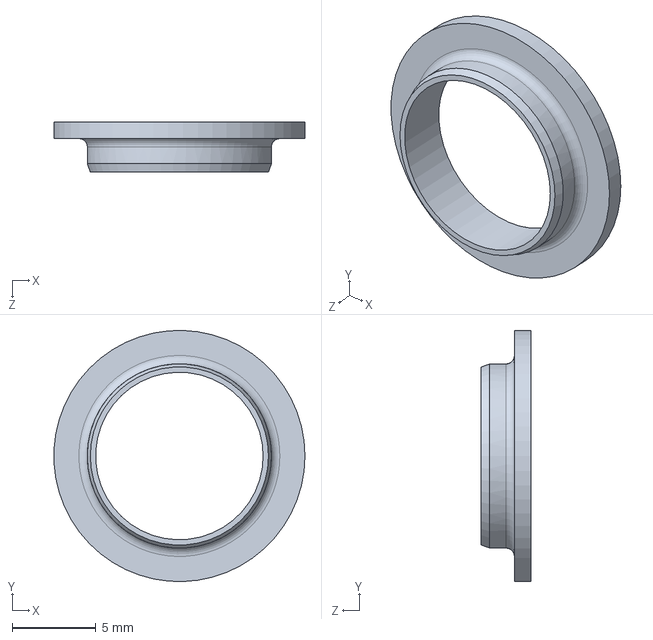
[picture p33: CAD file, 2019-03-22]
CAD/Ankle/gleitlager.SLDPRT
15.0 x 15.0 x 3.00 mm

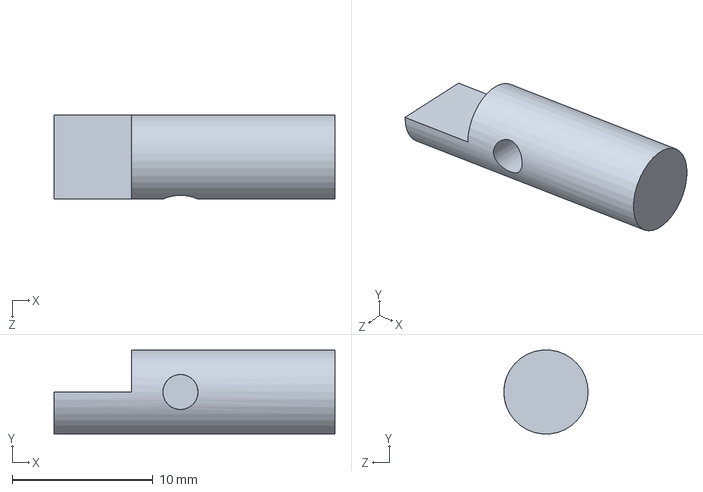
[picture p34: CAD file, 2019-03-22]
CAD/Gearbox/Motor_Shaft_out.SLDPRT
20.0 x 5.97 x 6.00 mm

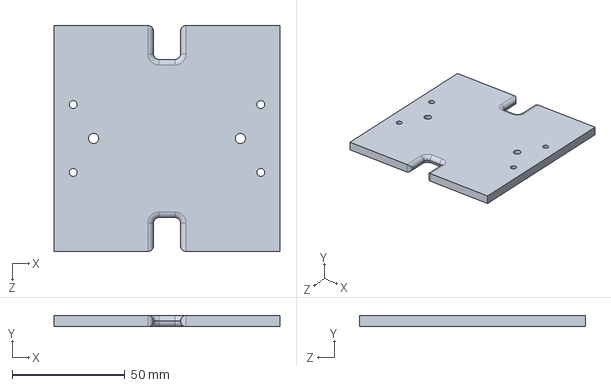
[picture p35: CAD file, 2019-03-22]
CAD/Gearbox/Spare_framework/Framework3.SLDPRT
100.0 x 5.00 x 100.0 mm

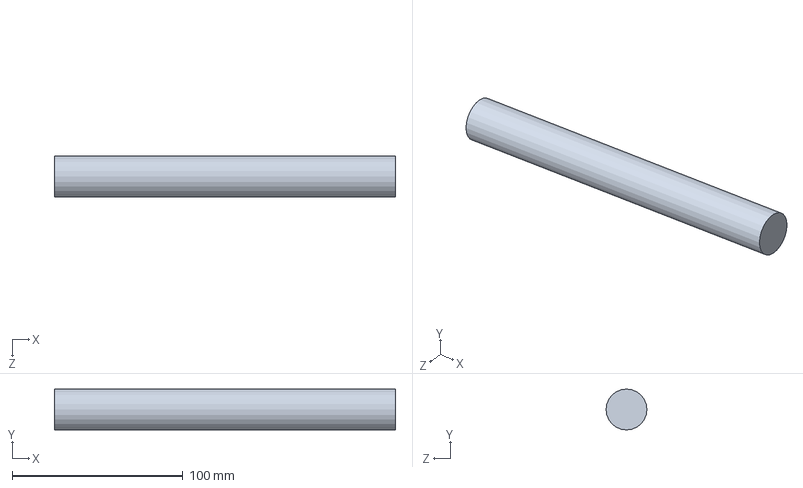
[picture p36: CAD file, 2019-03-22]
CAD/Mid_WoodShaft.SLDPRT
200.0 x 24.0 x 24.0 mm

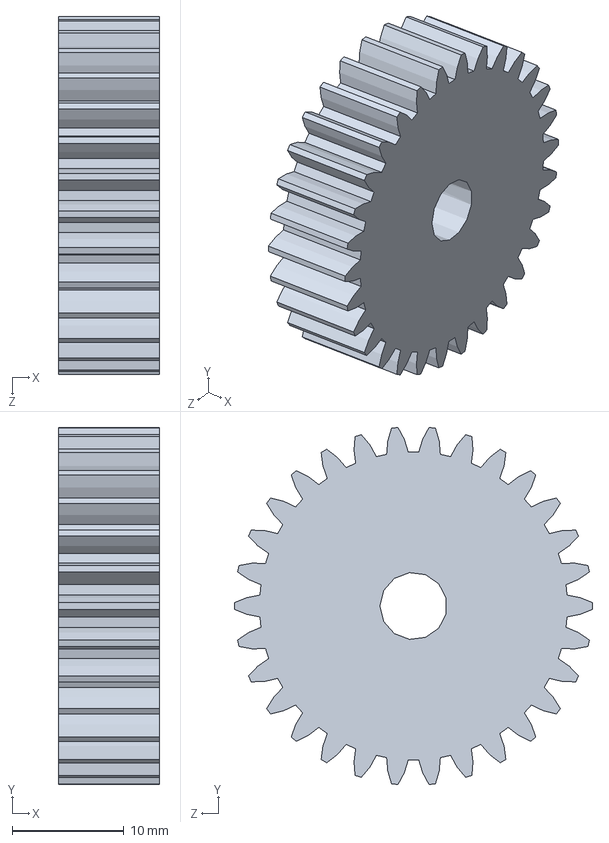
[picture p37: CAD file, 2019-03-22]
CAD/Gearbox/ISO - Spur gear 1M 30T 20PA 9FW ---S30A75H50L6.0N.sldprt
9.00 x 31.9 x 32.0 mm

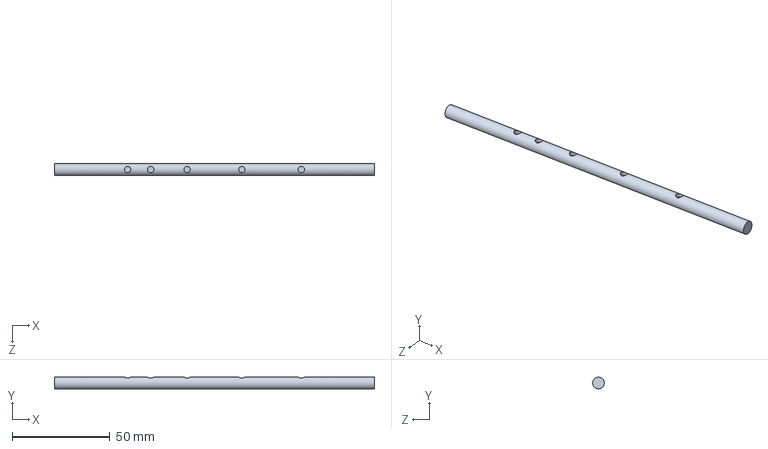
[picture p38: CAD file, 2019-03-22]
CAD/Shaft_right_left.SLDPRT
164.0 x 6.00 x 6.00 mm

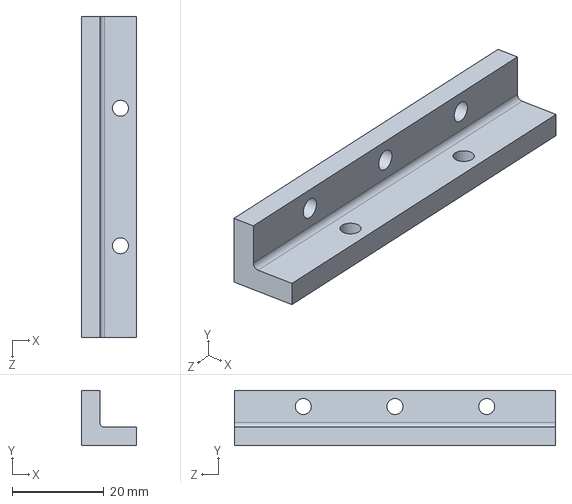
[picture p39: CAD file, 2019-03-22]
CAD/Gearbox/Spare_framework/bracket.SLDPRT
12.0 x 12.0 x 70.0 mm

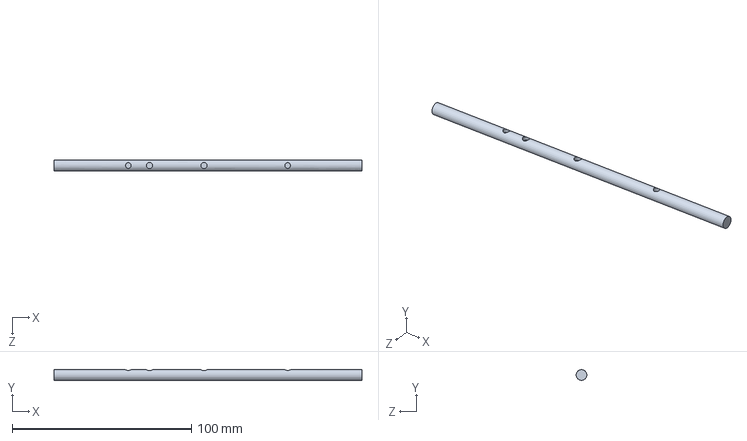
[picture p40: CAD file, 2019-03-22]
CAD/shaft_mid.SLDPRT
172.0 x 6.00 x 6.00 mm

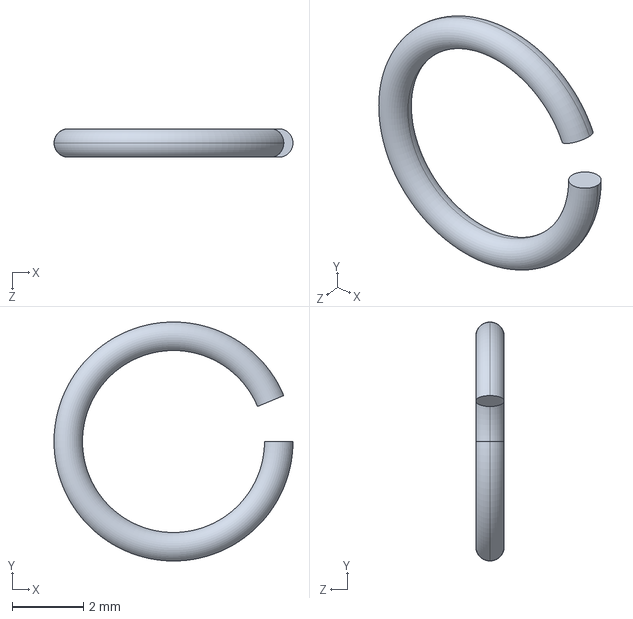
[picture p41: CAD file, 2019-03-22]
CAD/Gearbox/Snap ring A 6 DIN 7993.sldprt
6.70 x 6.70 x 0.797 mm

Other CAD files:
CAD/Gearbox/Spare_framework/framework2.SLDPRT
CAD/Gearbox/Middle_WoodPart.SLDPRT
CAD/Print_Hindfoot.SLDPRT
CAD/Gearbox/Winder.SLDPRT
CAD/20180603_Ankle/2018_06_02__10-02-27-338.ipt
CAD/20180603_Ankle/2018_06_02__10-02-27-338_1.ipt
CAD/20180603_Ankle/2018_06_02__10-02-27-338_2.ipt
CAD/20180603_Ankle/ANSI B18.2.4.2M - M5x0,8 - 8.ipt
CAD/20180603_Ankle/Assembly1.iam
CAD/20180603_Ankle/DIN 433 - 8,4.ipt
CAD/20180603_Ankle/DIN 988 - S9 x 15.ipt
CAD/20180603_Ankle/DoubleFork_lower.ipt
CAD/20180603_Ankle/Eye bolt GB 798 M5 x 25.ipt
CAD/20180603_Ankle/Foot_Ankl_Connector.ipt
CAD/20180603_Ankle/GBM_12_1.ipt
CAD/20180603_Ankle/ISO 4017 - M4 x 20DIN EN.ipt
CAD/20180603_Ankle/ISO 4017 - M8 x 25DIN EN.ipt
CAD/20180603_Ankle/ISO 4017 - M8 x 70DIN EN.ipt
CAD/20180603_Ankle/KBRM_12_1.iam
CAD/20180603_Ankle/Leg_Adapter.ipt
CAD/20180603_Ankle/WFM_1214_04_3.ipt
CAD/Ankle/2018_08_26__20-21-30-892_2.sldprt
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

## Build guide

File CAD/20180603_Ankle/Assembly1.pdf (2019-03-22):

setPageBoxes("Crop", 0, 0, [0,2000,2000,0]);

TITLE PART NO | Assembly1 REVISION DESIGNER | Till ENGINEER NOTES

THE INFORMATION AND/OR MATERIAL IN THIS DOCUMENT IS THE PROPERTY OF AND RESTRICTED INFORMATION AND/OR MATERIAL OF THE AUTHOR. THIS INFORMATION MAY NOT BE USED, REPRODUCED, PUBLISHED OR DISCLOSED TO OTHERS WITHOUT WRITTEN AUTHORIZATION. IT IS TO BE USED ONLY FOR MANUFACTURING ITEMS SPECIFIED WITHIN THE DOCUMENT.

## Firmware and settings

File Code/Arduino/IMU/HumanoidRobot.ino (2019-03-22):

/*
    Name:       HumanoidRobot.ino
    Author:     Marvin Gravert
*/
//This code works with the teensy 3.6 with 3 MPU 9250 on 3 different i2c Pins with 4.7k pull up resistors
//it prints the roll pitch yaw from the Earth->Sensor Transformation to the serial connection to be read
//by either the serial monitor/Simulink running on PC/Simulink running on the Pi.
//gyroscope and magnometer can be calibrated 

//General Improvements: 
//Better calibration. The magnometer calibration is rather poor, hence the yaw angle 
//is not correctly calcd by the sensor fusion . Only the offset in the gyro is calibrated and no calibration
//is done for the accelerometer. Though it didnt impact the results nearly as much as the magnometer.
//Switch to SPI, if i2c is  bottelnecking your speed
//Try a different sensor fusion algorithm. Magdwick is fine if you only have limited processor speeds. The teensy offers more than enough
//therefore it might be sensible to switch to a more computational intensive one who provides higher accuracy

//Possible Code Improvements: 
//MultiThreading, general code quality(eg enums,std::array/std::vector), optimazation, EEPROM to save calibration values 


#include <i2c_t3.h>
#include "MadgwickAHRS.h"
#include "MPU9250.h"

float pitch, yaw, roll, pitch2, roll2, yaw2,roll3,pitch3,yaw3;
float deltaT = 0.0f; //used for integration in sensor fusion
uint32_t lastUpdate = 0; // time of last sensor fusion update

MPU9250 mySensor(Wire);//PIN  SCL 19 SDA 18
MPU9250 mySensor2(Wire1);//PIN SCL 37 SDA 38
MPU9250 mySensor3(Wire2);//PIN SCL 3 SDA 4

MadgwickAHRS fusion1;
MadgwickAHRS fusion2;
MadgwickAHRS fusion3;

float accVal[3],accVal2[3],accVal3[3];
float gyroVal[3],gyroVal2[3],gyroVal3[3];
float magVal[3],magVal2[3],magVal3[3];

uint32_t currentTime,lastTimeMag,outputTimer,lastTimeSampledSens1 ,lastTimeSampledSens2 ,lastTimeSampledSens3 ;
uint32_t gyro1SampleDelay = 0,gyro2SampleDelay = 0,gyro3SampleDelay = 0;

uint32_t startTime = 0, accEndTime = 0, gyroEndTime = 0, magEndTime = 0;

typedef union
{
	float number;
	uint8_t bytes[4];
} FLOATUNION_t;


//currently all serial prints are commeted out due to sending the information to simulink on the pi. If you output to a serial monitor 
//i suggest you comment them in. So debugging is easier(such as scanning the i2c connection for i2c devices to check connection to the
//sensors. 
//Its highly recommended to use a serial monitor to run the calibration. In this implementation the values are printed to the serial monitor
//and then manually entered into the programm code. Calibration can be started by setting 'doCalibration' to true (located in setup)
void setup()
{
	Serial.begin(230400);
	while (!Serial);
	Wire.begin();//PINS 19/18  SCL:19 SDA 18
	Wire1.begin();//PINS 37/38  SLC 37 SDA 38
	Wire2.begin();//PINS 3/4  SCL 3 SDA 4
	Wire.setClock(400000L);
	Wire1.setClock(400000L);
	Wire2.setClock(400000L);

	//SCAN I2C PINS TO VERIFY CONNECTION

	//Serial.println("Sensor 1");
	//i2cScanner(&Wire);
	//Serial.println("Sensor 2");
	//i2cScanner(&Wire1);
	//Serial.println("Sensor 3");
	//i2cScanner(&Wire2);


	//INIT the sensors
	mySensor.initMPU();
	//Serial.println("Frist done");
	mySensor2.initMPU();
	//Serial.println("Second Done");
	mySensor3.initMPU();
	//Serial.println("Third Done");

	delay(1000);
	
	bool doCalibration = false;

	//either calibrate gyroscope/ magnometer or use values from previous calibration 
	if (doCalibration) {
		Serial.print("First the gyroscopes of all Sensors will be calibrated dont move the sensors");
		delay(2000);
		mySensor.calibrateGyro();
		mySensor2.calibrateGyro();
		mySensor3.calibrateGyro();
		Serial.println("Gyroscope calibration done. Printing values");
		Serial.println("Offset of gyroscope of Sensor on Pin 18/19");
		mySensor.printGyroOffset();
		Serial.println("Offset of gyroscope of Sensor on Pin 37/38");
		mySensor2.printGyroOffset();
		Serial.println("Offset of gyroscope of Sensor on Pin 3/4");
		mySensor3.printGyroOffset();
		delay(20000);
		Serial.println("Now the magnometer will be calibrated, starting with the sensor on Port 18/19");
		Serial.println("Get ready to move the sensor in elliptical curves. Start in roughly 5 seconds");
		mySensor.calibrateMag();
		Serial.println("First is done");
		delay(5000);
		Serial.println("Now the magnometer of the sensor on Port 37/38 will be calibrated");
		Serial.println("Get ready. Start in roughly 5seconds");
		mySensor2.calibrateMag();
		Serial.println("Second is done");
		delay(5000);
		Serial.println("Now the magnometer of the sensor on Port 3/4 will be calibrated");
		Serial.println("Get ready. Start in roughly 5seconds");
		mySensor3.calibrateMag();
		Serial.println("Third is done");
		Serial.println("Now the values will be printed");
		Serial.println("Sensor on Pin 18/19:");
		mySensor.printMagCalibration();
		Serial.println("Sensor on Pin 37/38");
		mySensor2.printMagCalibration();
		Serial.println("Sensor on Pin 3/4");
		mySensor3.printMagCalibration();
		Serial.println("Thats all calibration. Procedding as normal in 20seconds");
		delay(40000);
	}
	else {

		//in the following the values for the offsets and scale of the sensors derived from previous calibration are entered  
		//Sensor 1 
		float mag1ErrorScale[] = { 1.15f,1.25f,0.97f };
		float mag1Offset[] = { 16.0f,10.7f,-47.94f};
		float gyro1Offset[] = { 1.045f,0.795f,-0.94f};

		//Sensor 2
		float mag2ErrorScale[] = { 1.01f,1.055f,0.995f };
		float mag2Offset[] = { 19.14f,0.18f,-12.615f };
		float gyro2Offset[] = { 3.465f,1.29f, -0.77f };

		//Sensor 3
		float mag3ErrorScale[] = { 0.96f,1.02f,0.995f };
		float mag3Offset[] = { 9.045f,28.69f,-39.045f };
		float gyro3Offset[] = { -0.415f,0.03f, -0.0f };

		//Set the offset and errorscales
		mySensor.setMagCalibration(&mag1ErrorScale[0], &mag1Offset[0]);
		mySensor2.setMagCalibration(&mag2ErrorScale[0], &mag2Offset[0]);
		mySensor3.setMagCalibration(&mag3ErrorScale[0], &mag3Offset[0]);

		mySensor.setGyroOffset(&gyro1Offset[0]);
		mySensor2.setGyroOffset(&gyro2Offset[0]);
		mySensor3.setGyroOffset(&gyro3Offset[0]);

		// PrInt to monitor for debugging
		/*Serial.println("30seconds to compare, for debuggig purposes");
		mySensor.printMagCalibration();
		mySensor2.printMagCalibration();
		mySensor3.printMagCalibration();

		mySensor.printGyroOffset();
		mySensor2.printGyroOffset();
		mySensor3.printGyroOffset();
		delay(3000);*/
	}
	delay(500);

	currentTime = micros();

	mySensor.readAcc(&accVal[0]);
	mySensor.readGyro(&gyroVal[0]);
	mySensor.readMag(&magVal[0]);

	mySensor2.readAcc(&accVal2[0]);
	mySensor2.readGyro(&gyroVal[0]);
	mySensor2.readMag(&magVal2[0]);

	mySensor3.readAcc(&accVal3[0]);
	mySensor3.readGyro(&gyroVal3[0]);
	mySensor3.readMag(&magVal3[0]);


	//different times due to possibly different lowpass filter
	gyro1SampleDelay = mySensor.getGyroSampleDelayInMicro();
	gyro2SampleDelay = mySensor2.getGyroSampleDelayInMicro();
	gyro3SampleDelay = mySensor3.getGyroSampleDelayInMicro();

	lastTimeSampledSens1 = currentTime;
	lastTimeSampledSens2 = currentTime;
	lastTimeSampledSens3 = currentTime;
	lastTimeMag = currentTime;
	outputTimer = currentTime;
}
void loop()
{	
	currentTime = micros();
	//gyro updates its values 
	//Sensor 1 Pin 19/18
	if ((currentTime - lastTimeSampledSens1) > gyro1SampleDelay) {
		/*mySensor.readGyro(&gyroVal[0]);
		mySensor.readAcc(&accVal[0]);*/
		mySensor.readAccGyro(&accVal[0], &gyroVal[0]);
		lastTimeSampledSens1 = currentTime;
	}
	//Sensor 2 Pin 37/38
	if ((currentTime - lastTimeSampledSens2) > gyro2SampleDelay) {
		/*mySensor2.readGyro(&gyroVal2[0]);
		mySensor2.readAcc(&accVal2[0]);*/
		mySensor2.readAccGyro(&accVal2[0], &gyroVal2[0]);
		lastTimeSampledSens2 = currentTime;
	}
	////Sensor 3 Pin 3/4
	if ((currentTime - lastTimeSampledSens3) > gyro3SampleDelay) {
	/*	mySensor3.readGyro(&gyroVal3[0]);
		mySensor3.readAcc(&accVal3[0]);*/
		mySensor3.readAccGyro(&accVal3[0], &gyroVal3[0]);
		lastTimeSampledSens3 = currentTime;
	}
	//the mag is decoupeld from the other sensor and doesnot have a lowpass filter
	if ((currentTime-lastTimeMag)> 10000 ) {//mag updates with 100Hz=>0.01s aka 10000 us
		mySensor.readMag(&magVal[0]);
		mySensor2.readMag(&magVal2[0]);
		mySensor3.readMag(&magVal3[0]);
		lastTimeMag = currentTime;
	}

	currentTime = micros();
	
	//time difference for the integration in the fusion
	deltaT = ((currentTime - lastUpdate) / 1000000.0f);
	lastUpdate = currentTime;
	
	//note that magX and magY are swapped and the minus infront of magZ. This was done to allign the KOS of both sensors on the MPU
	fusion1.update(gyroVal[0], gyroVal[1], gyroVal[2], accVal[0], accVal[1], accVal[2], magVal[1], magVal[0], -magVal[2], deltaT);
	fusion2.update(gyroVal2[0], gyroVal2[1], gyroVal2[2], accVal2[0], accVal2[1], accVal2[2], magVal2[1], magVal2[0], -magVal2[2], deltaT);
	fusion3.update(gyroVal3[0], gyroVal3[1], gyroVal3[2], accVal3[0], accVal3[1], accVal3[2], magVal3[1], magVal3[0], -magVal3[2], deltaT);
	
	if (lastUpdate-outputTimer > 100000L){
		roll = fusion1.getRoll();
		pitch = fusion1.getPitch();
		yaw = fusion1.getYaw();
		roll2 = fusion2.getRoll();
		pitch2 = fusion2.getPitch();
		yaw2 = fusion2.getYaw();
		roll3 = fusion3.getRoll();
		pitch3 = fusion3.getPitch();
		yaw3 = fusion3.getYaw();

		//FOR SIMULINK ON PC 
		/*send2Simulink(roll);
		send2Simulink(pitch);
		send2Simulink(yaw);
		send2Simulink(roll2);
		send2Simulink(pitch2);
		send2Simulink(yaw2);
		send2Simulink(roll3);
		send2Simulink(pitch3);
		send2Simulink(yaw3);
		Serial.print('\n');*/

		//FOR SIMULINK RUNNING ON THE PI. Note the missing terminator
		//I suggest you comment out every other Serial.print that may execute 
		//so the serial read block wont be confused(mind you no terminator!!)
		send2Simulink(roll);
		send2Simulink(pitch);
		send2Simulink(yaw);
		send2Simulink(roll2);
		send2Simulink(pitch2);
		send2Simulink(yaw2);
		send2Simulink(roll3);
		send2Simulink(pitch3);
		send2Simulink(yaw3);

		//FOR SERIAL MONITOR

		/*Serial.print(roll);
		Serial.print(" ");
		Serial.print(pitch);
		Serial.print(" ");
		Serial.print(yaw);
		Serial.print("     ");
		Serial.print(roll2);
		Serial.print(" ");
		Serial.print(pitch2);
		Serial.print(" ");
		Serial.print(yaw2);
		Serial.print("     ");
		Serial.print(roll3);
		Serial.print(" ");
		Serial.print(pitch3);
		Serial.print(" ");
		Serial.print(yaw3);
		Serial.print('\n');*/


		outputTimer = lastUpdate;
	}
}	

void i2cScanner(i2c_t3 *Wire) {
	byte error, address;
	int nDevices;

	Serial.println("Scanning...");

	nDevices = 0;
	for (address = 1; address < 127; address++)
	{
		// The i2c_scanner uses the return value of
		// the Write.endTransmisstion to see if
		// a device did acknowledge to the address.
		Wire->beginTransmission(address);
		error = Wire->endTransmission();

		if (error == 0)
		{
			Serial.print("I2C device found at address 0x");
			if (address<16)
				Serial.print("0");
			Serial.print(address, HEX);
			Serial.println("  !");

			nDevices++;
		}
		else if (error == 4)
		{
			Serial.print("Unknown error at address 0x");
			if (address<16)
				Serial.print("0");
			Serial.println(address, HEX);
		}
	}
	if (nDevices == 0)
		Serial.println("No I2C devices found\n");
	else
		Serial.println("done\n");

	delay(5000);           // wait 5 seconds for next scan
}

void send2Simulink(float tt) {
	//the input argument is sent byte for byte to the serial ports (little endian)
	FLOATUNION_t fa;
	fa.number = tt;
	for (int i = 0; i<4; i++)
	{
		Serial.write(fa.bytes[i]);
	}
}
